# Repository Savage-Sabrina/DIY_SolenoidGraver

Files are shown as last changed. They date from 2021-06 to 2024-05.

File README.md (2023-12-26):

# GraverController
An Arduino Nano based Mosfet controller for solenoid graver.

I got into jewelry making in 2010 to pay for my college expenses. After graduating as a mechanical engineer I realized part of my knowledge should not be wasted and should be applied into something I like.
After looking into the options on a pneumatic graver I realized it was either too expensive or bulky. 
I would not have space for a compressor because I lived in a small room on a shared house.
This is, then, my approach to a solenoid based graver machine.
You could check other approaches like https://github.com/alastair-duncan/SuperEZGraver,  https://www.youtube.com/channel/UCE2rGFm1-xs-WIEHfY1enjA and also my favorite interface https://github.com/Billiam/gravedriver.

The focus I want to bring is of a solenoid for stone setting and fine work, although the power is only limited by the solenoid chosen, buck converter and MOSFET.
You can check videos of it working on [YouTube](https://www.youtube.com/user/selvalss/videos) and the results I got with it [here](https://youtu.be/fjaF6JF7hFk). All tests were performed in the Direct Mode, as programmed in the _Controller_ section below.

If you are handy in terms of Arduino coding and making breadboard circuits this will be super easy to make and program, this will cover mainly a way to make the controller and handpiece with hobby parts. There is also the option to build a custom board with everything integrated already, which is inside the [custom board folder.](https://github.com/Savage-Sabrina/DIY_SolenoidGraver/tree/master/Schematic/Custom%20board%V2) This last option has the benefit of being tidy and you have also all the 3d files to make it look good and functionally tested.

# **Starting the project**
I am sharing this to provide more information on what might be necessary to build your own solenoid engraving machine.

With this I assume that you are:

1. Old enough to know your limitations
1. Liable to your own choices
1. Knowledgeable in electronics

None of the links shared in this guide are affiliate links.

The intent with this guide is to provide knowledge and maybe a bit of opportunity to those who cannot afford a commercial machine or do not have access to the means necessary to get hold of one. I know how it feels to “plan” to buy a machine if we save 50% of our income for the next 5 years to be able to afford the basic version without accessories to run it. No infringement of copyright or patent is intended.

---
# **The solenoid**
The solenoid used should be strong enough to provide the magnetic field but light enough not to be bulky and on the way when engraving. The voltage rating as well as the duty cycle should be compatible with the usage.

A better solution would be to have a commercially available solenoid as the impact source, this would provide some maintenance possibilities. A good choice would be the 12V version of the solenoid 1335. [ITS-LZ-1335-D-24VDC](https://www.elpro.org/gb/red-magnetics-its-lz-series/32677-its-lz-1335-d-24vdc.html) solenoid (The name 1335 means 13mm X 35mm, some companies use the 13x27 which disconsiders the thread length).

The disadvantage of this solenoid is that the diameter of the impact shaft will make it crooked after approx. 300h of use in maximum load (based on tests with impact on an upstanding weight of 40 grams), which is reasonably long but not something to be disregarded.

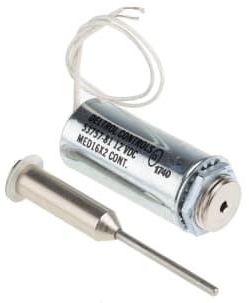
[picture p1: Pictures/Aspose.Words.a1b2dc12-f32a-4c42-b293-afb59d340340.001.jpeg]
53757-81 | Deltrol Linear Solenoid, 12 V dc, 35.9N, 1.4 (Stroke N @ 0.75 in), 25.4 (Dia.) x 60.33 mm | RS
ITS-LZ 1335-D – RED MAGNETICS

Another disadvantage of this model is that the solenoid cannot release enough heat and might overheat, solutions to this are:

1. Make a heatsink for it.
2. Manufacture an open handpiece to allow airflow.
3. Usage of a [Flyback Diode](https://en.wikipedia.org/wiki/Flyback_diode) to remove voltage spikes from the coils. **(This one is actually mandatory)**

## **Custom Solenoid**
If you intend to produce your own solenoid there are some considerations that should be put in place that will make your life easier:

1. The plunger for the solenoid should be floating so as to regulate the amplitude of the impact, a smaller amplitude can lead to faster and more delicate impacts, a greater amplitude can be good for the bezel setting or steel engraving. Free floating solenoids like the 1335 above are regulated by putting some limiter in the back to reduce or increase its amplitude like some sort of screw.
1. The plunger weight should be around 6-8 grams to allow flexibility of energy and speed. A 6 g plunger with the right spring and coil can get up to 60 HZ with an amplitude of 3mm. An 8 gram plunger can even engrave steel, with a 5mm amplitude.
1. An open design of the coil to dissipate the heat will make it last and allow it to use the handpiece for longer since it won’t be too hot.
1. Do not forget the flyback diode as mentioned before.
1. Make sure the wire for the coil can handle the voltage and current to avoid melting and increased temperature.

A plunger with the dimensions below and a handmade spring with a 0.2mm wire can yield great results. The advantage of this is to manufacture something that is exclusive to your needs. With these dimensions I was able to engrave steel and also fine tune it to set 1.3mm stones pave style. The 0.7 mm step is the place to fit the spring, this solenoid should be powered at 12V 25% duty cycle maximun.



---
# **The handpiece**
After some iterations and failures I want to bring some insights to the design if you want to use the one developed or project your own.



For a design that can be assembled with minimal tools and an optional 3d printer you can check my page. The good thing about being open is that we can be sure that people will create better options than our own idea.



This design allows you to use a 1335 solenoid and a 9/16 inch brass tube from K&S to enhance the structure of the parts. The tube that fits the [GRS tool holder](https://grs.com/product/grs-quickchange-handle/) is a [5/16 inch tube from K&S metals](https://ksmetals.com/products/br029-5-16?_pos=1&_psq=5%2F16&_ss=e&_v=1.0), it can be used as a sleeve to make the plast stronger and for the collet to slide easier. If you want to make your own design this tube fits in a 3d printed hole of 7.2mm better due to the approximation of a circle to a polygon.
For a better fit, with some adjustments, the standard tube 3/8" 16 gauge will have a tight grip on the GRS collet. Although not ideal it can be sanded up to the allow movement when hit. The tube can be found on steel, which is a bit harder to work but more durable, or brass.
Some other options can be considered, like using machining services offered online for a perfect fit with the internal dimension of 1/4" or 6.35 mm. With this approach you can not only make your own handpiece but also your own quick change handle. The sleeve should look like the image below.

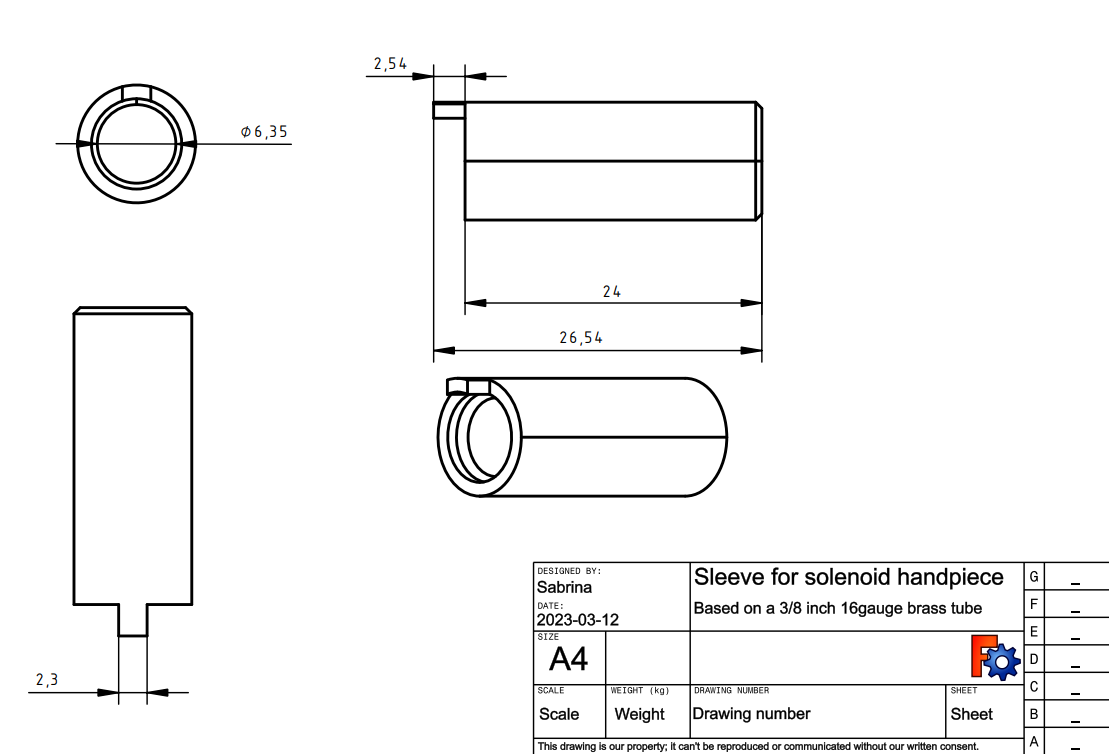
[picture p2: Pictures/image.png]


This thicker sleeve would replace the thin K&S Tube pirctured below. I got better results with this snaded version of the brass tube.

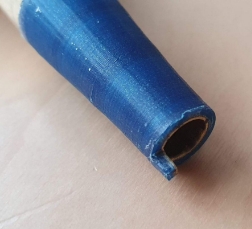
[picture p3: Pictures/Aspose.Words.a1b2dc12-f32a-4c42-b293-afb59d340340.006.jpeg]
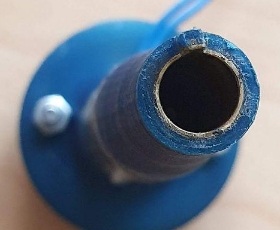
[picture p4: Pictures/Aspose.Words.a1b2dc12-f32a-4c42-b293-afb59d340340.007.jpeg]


---
# **Controller**
For the controller I went with 2 different platforms, one with a Raspberry PI PICO to have a touch interface and better PWM controls and an Arduino to make things cheaper and accessible to the majority of people. I projected a custom board that contains all the components in one, the board is only aimed at people that really know what they are doing, you can find it in the [custom board folder](https://github.com/Savage-Sabrina/DIY_SolenoidGraver/tree/master/Schematic/Custom%20Board%20V2)

In this document I will handle only the Arduino version of the controller as it is the simplest and readily available. For the Raspberry version I realized that the version of the software installed as well as the version of MicroPython impacted on the controls and had some bugs and differences due to the GPIO.PWM frequency limitations. The parts referenced are just a guideline, they are not exclusive or irreplaceable.

Necessary parts:

1. Arduino (The cheapest one that will work is the [Nano](https://store.arduino.cc/products/arduino-nano), since it’s an open platform you can use a “generic” version)
1. [Mosfet board](https://www.amazon.com/HiLetgo-IRF520-MOSFET-Arduino-Raspberry/dp/B01I1J14MO) (Learn more about MOSFETS [Here](https://dronebotworkshop.com/transistors-mosfets/))
1. Expression pedal ([This](https://www.thomann.de/se/maudio_expression_pedal.htm) was the cheapest in Europe and worked like a charm)
   1. Or a [potentiometer pedal](https://thepihut.com/products/foot-pedal-potentiometer-sewing-machine-speed-controller).
1. PSU (A laptop PSU can fulfill the needs of almost everyone, I could even engrave steel with a 18V 4A)
1. 2X [Potentiometers](https://thepihut.com/products/gravity-analog-rotation-potentiometer-sensor-v1-for-arduino)

Optional parts:

1. [Buck converter](https://thepihut.com/products/dc-dc-power-module-25w) or [this](https://www.amazon.ca/Lysignal-LM2596-Supply-Adjustable-Converter/dp/B074J4NXCM), Make sure the output voltage is set to 5V before you connect the components (Makes only one PSU enough instead of 2 connectors)
1. [Buttons](https://thepihut.com/products/stemma-wired-tactile-push-button-pack-5-color-pack) (If you are going for a more complete programming they are necessary)
1. [Switch](https://thepihut.com/products/mini-panel-mount-dpdt-toggle-switch) (To make it easier to turn the power from the PSU on and off)
1. [Breadboard](https://thepihut.com/products/raspberry-pi-breadboard-half-size) (Makes it easier to connect the wires)

For the Arduino pinout any variant can be used. The model represented in the schematics is the Arduino Nano.

The schematics of the connection is as shown below:



The complete schematics are [in the shared folder](https://github.com/Savage-Sabrina/DIY_SolenoidGraver/tree/master/Schematic) with a .PDF or .PNG file.

What has to be done when assembling it safelly:

1. Check if all the connections are in place apart from the PSU.
1. Connect the Arduino to the pc and use the ArduinoIDE interface to check the code.
1. Upload the [Arduino code](https://github.com/Savage-Sabrina/DIY_SolenoidGraver/blob/34cf9a5d53c3de1b95fa2ae14cb3af24335a9292/Arduino%20Code/BetaVersion0.2LCD+VariableFootPedal.ino) for the desired control, which will have 3 modes:
   1. Frequency mode, you choose the frequency and the duty cycle with the potentiometers, the pedal will change the power input according to the selection, the information is shown on the LCD.
   1. Pulse mode, the handpiece will give a certain amount of pulses according to frequency and duty, the pulses go to maximum power at start and stop for half a second then continue within a defined interval.
   1. Direct mode, the handpiece goes to maximum power instantaneously according to duty and frequency selected.
1. Test the board without the solenoid handpiece or PSU in place and look at the LED of the mosfet to look for it blinking.
2. Use a weaker PSU just to check the main connections.
3. Assemble everything and test it for a split second to verify short circuits in your assembled handpiece. To avoid heating of the handpiece don't forget the Flyback diode.
4. Enjoy!

---
# **Custom board V2**
The custom board below has already the connections made and it's only up to you to connect the power lines, pedal, graver and your own Arduino Nano. You can order the boards on PCB manufacturers that send it to the whole world like PCBWay and JLCPcb.
You can find the design on the [custom board folder.](https://github.com/Savage-Sabrina/DIY_SolenoidGraver/tree/master/Schematic/Custom%20Board%20V2)
The design is divided in 2 parts, the Arduino Nano Board and the Controll Board with buttons and potentiometers as shown below:
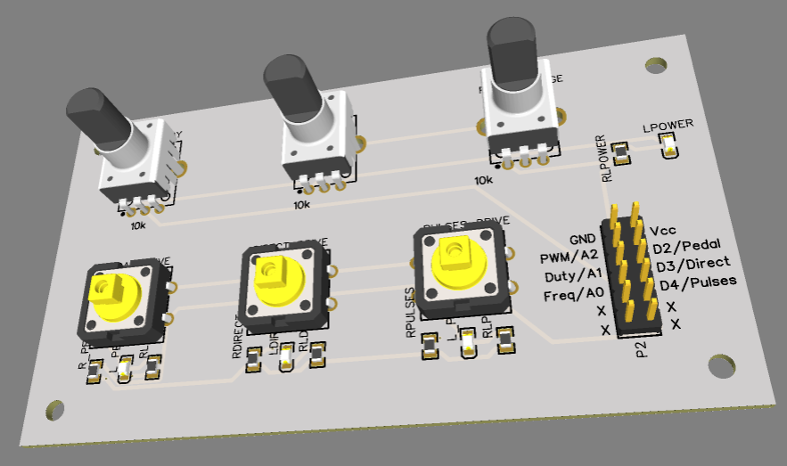
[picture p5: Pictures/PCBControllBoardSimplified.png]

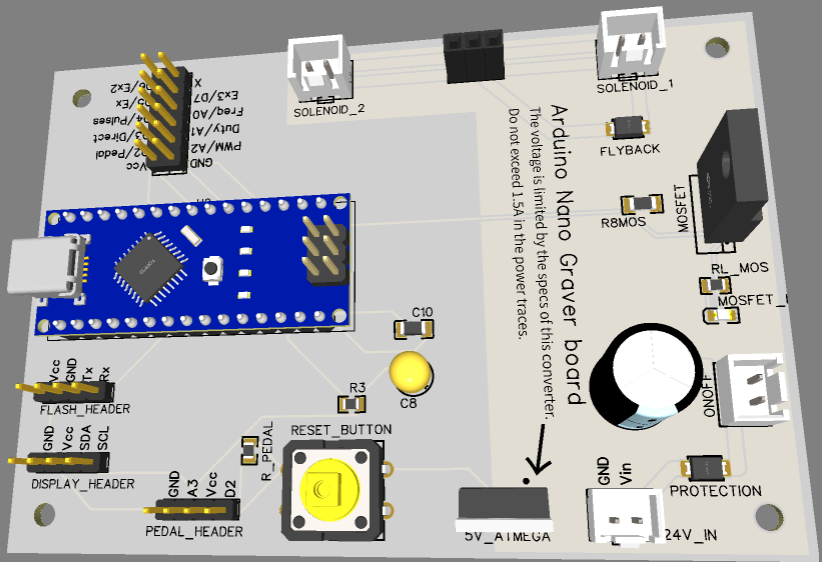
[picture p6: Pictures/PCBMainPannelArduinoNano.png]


***
# **Final considerations**

If you feel that something should be changed or is wrong feel free to inform me or to perform your own modifications.
Suggestions are always welcome, I had a brief contact with a professional grade engraver in order to feel the impact in the hand and tool behavior which was not enough to feel the nuances of the machine.
If you need assistance with the project please message me on reddit u/Weird\_Singularity.

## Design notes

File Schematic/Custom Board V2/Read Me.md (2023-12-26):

This version of the board is the final developed for the Arduino Nano.
I realized that not everyone had the knowledge to burn a bootloader on the MCU so the arduino Nano option was the best option.
The board can handle the 18V 1.5A on the power traces.
The code is on the Arduino Code folder in a way that is shown on the youtube video.

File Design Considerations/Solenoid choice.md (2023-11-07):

For a full in depth review of the solenoid choices please watch the video about the perks and configuration of each magnet below. [Youtube video about the solenoids and handpiece](https://www.youtube.com/watch?v=2lFhfABcx04)

The first solenoid I tested was the smallest 5v solenoid i could get just to prove the concept. [Small solenoid](https://www.adafruit.com/product/2776)
small 5V solenoid

It was really weak and I realized that I was supposed to know about how a graver would work.
I found some options to understand better the impact force on this video from [Shaun Hughes](https://www.youtube.com/watch?v=1zzqaAYdvdQ&ab_channel=ShaunHughesEngraving) and from that went on the look for a solenoid that would give me the aproximate ammount of travel for this to happen.

The first solenoid I went to was a popular [jf-0530B](https://www.aliexpress.com/item/32777233179.html) (12V, 300mA) that had quite a punch but a long stroke and long body, making the handpice too bulky. Maybe to replace a hammer and chisel for someone with a hand disabilyty might be awesome.
jf-0530b

The second solenoid used was the one from [Adafruit](https://www.adafruit.com/product/413),with 12V and 250mA it was a little wider. It had strong strokes but a lower frequency of oscilation. (https://www.adafruit.com/product/413)
adafruit solenoid

I had an intermediary solenoid (12V, ~900mA) that was open and could dissipate better the heat while having a good impact force. Like the on on the [link](https://www.aliexpress.com/item/4000013441378.html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,searchweb201602_,searchweb201603_), unfortunatelly this also had a low frequency and to make it fit on an easy handpiece was a hassle.

Used a [linear cylindrical solenoid](https://www.red-magnetics.com/en/product-groups/linear-solenoids/cylinder-solenoids/its-lz-1335-d/) to have better control on the stroke length and natural frequency of the solenoid. Got this one on the 12V and 24V variants. After testing for some time I realized my tolerances were too tight as the shaft had bended and shortened with the impact. I would need something more robust as an impact shaft to withstand the continuous impacts on the solenoid.

I had to find an intermitent duty, 12-24V solenoid that would be good to use and easy to maintain. Found a [perfect match](https://www.youtube.com/watch?v=ASwVTQaLLGc&t=62s&ab_channel=IndexBraille) with no avail to get my hands on it as the complay would not sell unless I had the machine that would use it. So I had to find something similar on the internet. After going back and forth with the manufacturer I got a [replacement solenoid](https://www.aliexpress.com/item/32996508114.html?spm=a2g0s.9042311.0.0.53844c4ddj9pqp) that would be the same function as the perfect match I wanted. Cut the shaft to length and got a better frequency of oscilation on the solenoid and better impact force with 19V. But it would still overheat. Thats were I came to realization that it's better to make my own solenoid. The saft from the cheap solenoid is percet to make my own. And this is the next step on the making of the handpiece.


Extras:
How to make a solenoid: https://www.instructables.com/How-to-Make-Solenoid-at-Home/
Mosfet control for NERF: https://www.youtube.com/watch?v=hRxzcRwo_3U&ab_channel=Valour%27sBlasters

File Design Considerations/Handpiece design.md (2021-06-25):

To start the desig of thehandpiece I took into consideration the design of current pneumatic gravers. To keep standard dimensions went first on some commercial models, [technical drawings](https://www.chipmaker.ru/topic/132834/?page=4) and details I found on some [forums](https://www.jportal.ru/forum/forum76/topic15895/).
I will skip here the previous considerations of the handpiece from the solenoid choice on the other folder of this project, therefore I will only cite here the design based on the last solenoid.

1 - The easiest collet to use.
2 - The strength of the connection from the 3D printed version to the piston tube.
3 - Heat dissipation.
4 - Possibility of control the stroke lenght on a free piston solenoid.

1 - The easiest collet to use that was [available](https://www.cooksongold.com/Jewellery-Tools/GRS-Quick-Change-Traditional-Tool-Holder-For-3.45mm-Shank-Gravers----Pack-of-3-prcode-998-G231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) was the GRS collet that had 6.35mm diameter or 1/4 inch. (I don't like these imperial measurements I would rather have a collet with a round mm number that would make it easier to adapt something) I had it available on my country since it's a global and present company.

2 - To resolve the strengh of the connection on the plastic of the 3D printed handpiece, avoiding it breaking because of the constant impact and rubbing on the plastic, I found online a [hobbist brass tube](https://www.hobbylinc.com/k-s-round-brass-tube-9:32-hobby-and-craft-metal-tubing-8132) with the correct internal diameter matching the external diameter of the collet. This way I would insert the brass tube inside the 3D printed handpiece to hold the collet and make a smoother movement while also strenghtening the handpiece on the most critical place.

3 - Heat dissipation would be done by having openings on the faces that had the least ammount of stress. Since the PLA used would retain the heat it would not be good to have it carry the heat away. For now the heat will go to all he sides instead of a channeled air path.

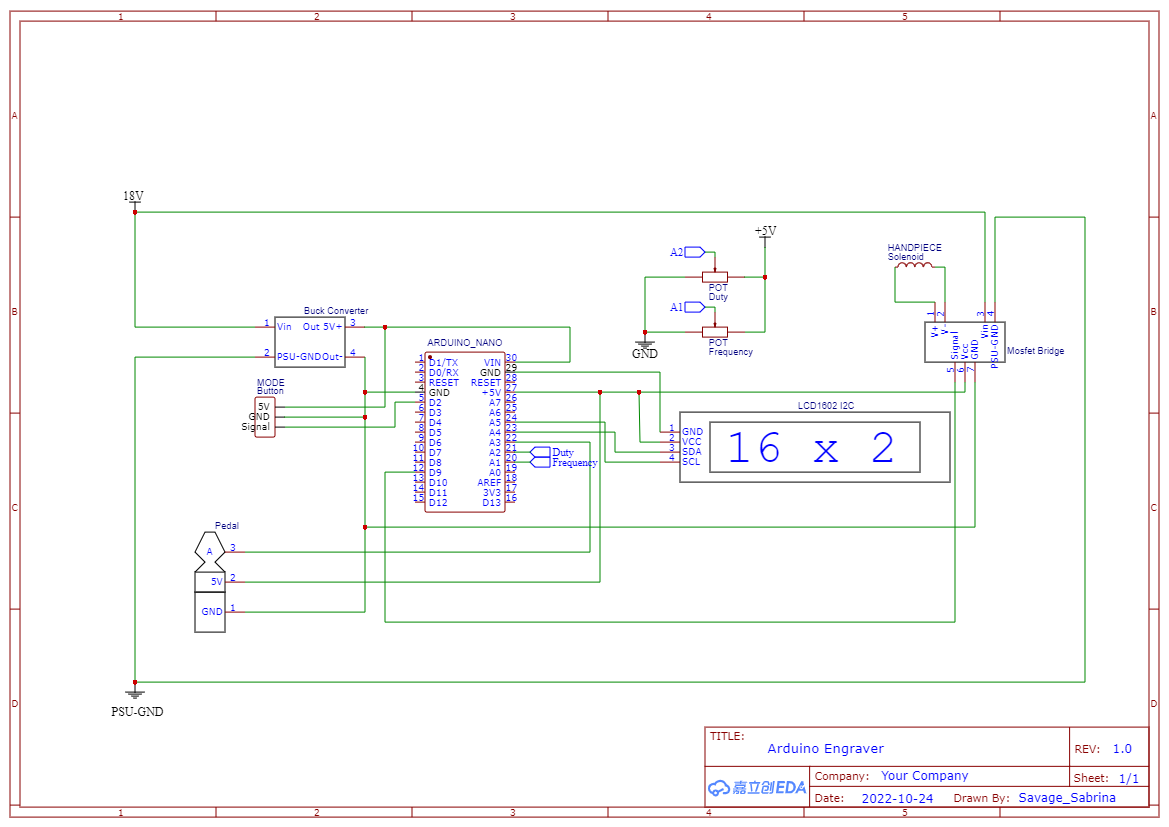
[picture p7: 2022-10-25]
Schematic/Schematic_ArduinoNanoEngraver_2022-10-24.png

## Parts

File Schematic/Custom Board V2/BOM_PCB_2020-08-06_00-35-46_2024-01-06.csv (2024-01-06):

ID | Name | Designator | Footprint | Quantity | Manufacturer Part | Manufacturer | Supplier | Supplier Part | Price | Pins | 3DModel | Contributor | LCSC Assembly | SMT Type | image | link
1 | 17-21SUYC/TR8 | LDIRECT,L_PEDALDRIVE,L_PULSES,LPOWER | LED0805-RD | 4 | 17-21SUYC/TR8 | KENTO | LCSC | C2296 | 0.012 | 2 | LED0805-RD | lcsc | Yes | Basic | //image.lceda.cn/szlcsc/C2296.jpg | https://item.szlcsc.com/255094.html
2 | 1K | RDIRECT,RPULSES,R_PEDALDRIVE | R0805 | 3 | 0805W8F1001T5E | UniOhm | LCSC | C17513 | 0.002 | 2 | R0805_L2.0-W1.3-H0.6 | layout | Yes | Basic |  | https://item.szlcsc.com/142685.html
3 | 75 | RLDIRECT,RLPEDALDRIVE,RLPULSES | R0805 | 3 | 0805W8F750JT5E | UniOhm | LCSC | C20638 |  | 2 | R0805_L2.0-W1.3-H0.6 | layout | Yes | Basic |  | https://item.szlcsc.com/142685.html
4 | 10K | DUTY,FREQUENCY,PWM/VOLTAGE | RES-TH_RK09K1130AAU | 3 | RK09K1130AAU | ALPS Electric | LCSC | C202373 | 0.624 | 5 | RES-TH_RK09K1130AAU | LCSC |  |  |  | https://list.szlcsc.com/catalog/556.html
5 | B3F-4055 | DIRECT_DRIVE,PEDAL_DRIVE,PULSES_DRIVE | KEY-TH_4P-L12.0-W12.0-P5.00-LS13.4-EH | 3 | B3F-4055 | OMRON | LCSC | C84931 | 0.088 | 4 | KEY-TH_4P-L12.0-W12.0-H7.5-LS12.5-P5.0 | lcsc |  |  |  | https://item.szlcsc.com/84377.html
6 | Header-Male-2.54_2x6 | P2 | HDR-TH_12P-P2.54-V-M-R2-C6-S2.54 | 1 |  |  | LCSC | C66689 | 0.038 | 12 | HDR2.54-M-LI-2X6P | lcsc |  |  |  | https://lcsc.com/eda_search?q=C66689&%26type=1&ref=editor
7 | 75 | RLPOWER | R0805 | 1 | 0805W8F750JT5E | UniOhm | LCSC | C20638 |  | 2 |  |  | Yes | Basic

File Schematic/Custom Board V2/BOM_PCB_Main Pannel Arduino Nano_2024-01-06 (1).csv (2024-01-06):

ID | Name | Designator | Footprint | Quantity | Manufacturer Part | Manufacturer | Supplier | Supplier Part | Price | Pins | 3DModel | Contributor | JLCPCB Part Class | LCSC Assembly | SMT Type | image | link
1 | ARDUINO_NANO | U2 | COMM-TH_ARDUINO_NANO | 1 | ARDUINO_NANO | null | LCSC | C9900017879 |  | 30 | ARDUINO_NANO | lcsc | Extended Part |  |  |  | https://lcsc.com/eda_search?q=C9900017879&%26type=1&ref=editor
2 | L7805ACV | 5V_ATMEGA | TO-220-3_L10.0-W4.5-P2.54-T | 1 | L7805ACV | ST(意法半导体) | LCSC | C192854 | 0.352 | 3 | TO-220-3_L10.0-W4.5-P2.54 | LCSC | Extended Part |  |  |  | https://item.szlcsc.com/88574.html
3 | XHB-2A Connector | 24V_IN,ONOFF,SOLENOID_1,SOLENOID_2 | CONN-TH_XHB-2A | 4 | XHB-2A Connector | BOOMELE | LCSC | C57981 | 0.01 | 2 | CONN-TH_XHB-2A | 立创EDA官方封装库 |  |  |  | //image.lceda.cn/szlcsc/C57981.jpg | https://item.szlcsc.com/59018.html
4 | 100nF | C10 | C1206 | 1 | CL31B104KBCNNNC | SAMSUNG | LCSC | C24497 | 0.014 | 2 | C1206_L3.2-W1.6-H1.3 | layout |  | Yes | Basic |  | https://item.szlcsc.com/89171.html
5 | 10uF | C8 | CAP-TH_BD5.0-P2.5-D0.5-FD | 1 | C10uF63V2.5mm5x11mm | ReliaPro | LCSC | C32455 | 0.015 | 2 | CAP-TH_BD5.0-H7.5-P2.5 | lcsc |  |  |  |  | https://item.szlcsc.com/292492.html
6 | 100uF | C9 | CAP-TH_BD10.0-P5.00-D1.0-FD | 1 | 10X17 100V100uf | ValuePro | LCSC | C3336 | 0.092 | 2 | CAP-TH_D10.0-H16.0-P5.00 | lcsc |  |  |  |  | https://item.szlcsc.com/44833.html
7 | Header-Male-2.54_1x4_C124378 | DISPLAY_HEADER,FLASH_HEADER,PEDAL_HEADER | HDR-TH_4P-P2.54-V | 3 | 210S-1*4P L=11.6MMGold-plated black | Ckmtw | LCSC | C124378 | 0.04 | 4 | HDR-M-2.54_1x4 | LCSC |  |  |  |  | https://lcsc.com/product-detail/Pin-Header-Female-Header_Made-in-China-Made-in-China-Headers-Pins1-4-pitch2-54mm_C59481.html
8 | 1N4004F | FLYBACK,PROTECTION | SMAF_L3.5-W2.6-LS4.7-RD | 2 | 1N4004F | SK | LCSC | C122842 | 0.006 | 2 | SMAF_L3.5-W2.6-H1.2-LS4.7 | 官方封装库 |  | Yes | Extend |  | https://item.szlcsc.com/125168.html
9 | IRL520PBF | MOSFET | ITO-220AB-3_L10.2-W4.5-P2.60-L | 1 | IRL520PBF | VISHAY | LCSC | C145199 | 1.316 | 3 | ITO-220AB-3_L10.2-W4.5-H15.0-P2.60 | LCSC |  |  |  |  | https://item.szlcsc.com/387411.html
10 | Header-Female-2.54_1x3 | P1 | HDR-TH_3P-P2.54-V-F | 1 | 2.54-1*3P母 | BOOMELE(博穆精密) | LCSC | C146243 | 0.057 | 3 | HDR2.54-F-LI-1X3P | lcsc | Extended Part |  |  |  | https://lcsc.com/eda_search?q=C146243&%26type=1&ref=editor
11 | 10K | R3 | R0805 | 1 | 0805W8F1002T5E | UniOhm | LCSC | C17414 | 0.001 | 2 | R0805_L2.0-W1.3-H0.6 | layout |  | Yes | Basic |  | https://item.szlcsc.com/142685.html
12 | 75 | RL_MOS | R0805 | 1 | 0805W8F750JT5E | UniOhm | LCSC | C20638 |  | 2 | R0805_L2.0-W1.3-H0.6 | layout |  | Yes | Basic |  | https://item.szlcsc.com/142685.html
13 | 1K | R_PEDAL | R0805 | 1 | 0805W8F1001T5E | UniOhm | LCSC | C17513 | 0.002 | 2 | R0805_L2.0-W1.3-H0.6 | layout |  | Yes | Basic |  | https://item.szlcsc.com/142685.html
14 | 1K | R8MOS | R1206 | 1 | 1206W4F1001T5E | UniOhm | LCSC | C4410 | 0.003 | 2 | R1206_L3.2-W1.6-H0.6 | layout |  | Yes | Basic |  | https://item.szlcsc.com/311874.html
15 | B3F-4055 | RESET_BUTTON | KEY-TH_4P-L12.0-W12.0-P5.00-LS13.4-EH | 1 | B3F-4055 | OMRON | LCSC | C84931 | 0.088 | 4 | KEY-TH_4P-L12.0-W12.0-H7.5-LS12.5-P5.0 | lcsc |  |  |  |  | https://item.szlcsc.com/84377.html
16 | 17-21SUYC/TR8 | MOSFET_L | LED0805-RD | 1 | 17-21SUYC/TR8 | KENTO | LCSC | C2296 | 0.012 | 2 | LED0805-RD | lcsc |  | Yes | Basic | //image.lceda.cn/szlcsc/C2296.jpg | https://item.szlcsc.com/255094.html
17 | Header-Male-2.54_2x6 | P2 | HDR-TH_12P-P2.54-V-M-R2-C6-S2.54 | 1 |  |  | LCSC | C66689 | 0.038 | 12 | HDR2.54-M-LI-2X6P | lcsc |  |  |  |  | https://lcsc.com/eda_search?q=C66689&%26type=1&ref=editor

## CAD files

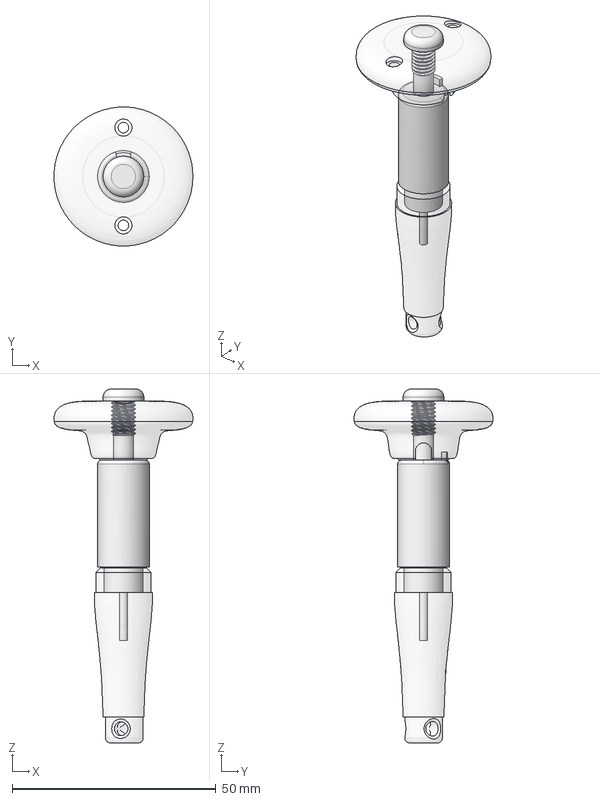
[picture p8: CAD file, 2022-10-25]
CAD files/Assembly new handpiece 1335.FCStd
34.1 x 34.1 x 86.9 mm
Solenoid 1335_001
Collet GRS_001
Front cap_001
BackBody Part_001
Back Lid Part_001
Screw cap_001

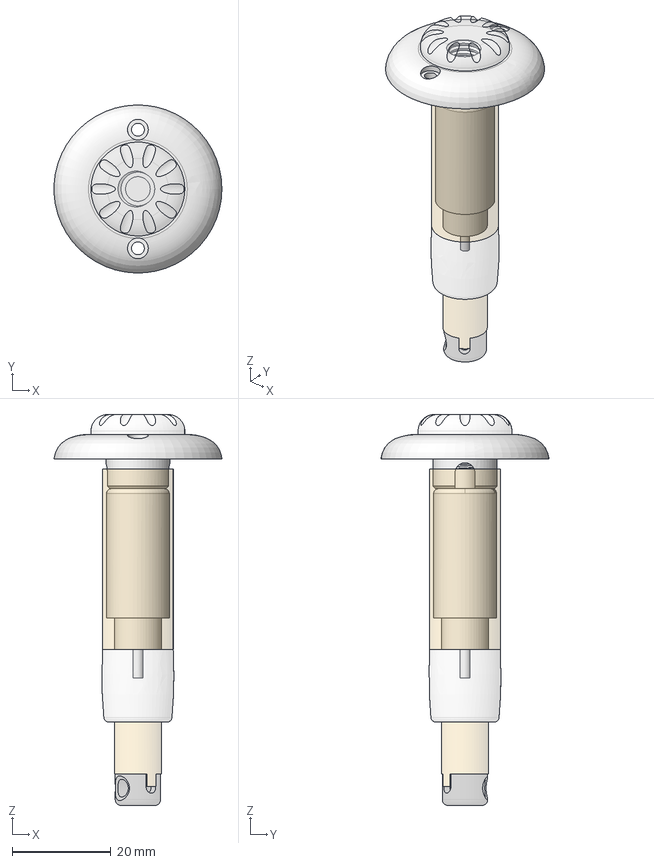
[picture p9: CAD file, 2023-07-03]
CAD files/Thick sleeve/Assembly new handpiece 1335.FCStd
34.0 x 34.0 x 79.1 mm
Solenoid 1335_001
Collet GRS_001
Back Lid Part_001
Front cap thick sleeve_001
3 8 inch sleeve_001
Screw cap_001
Tube_001

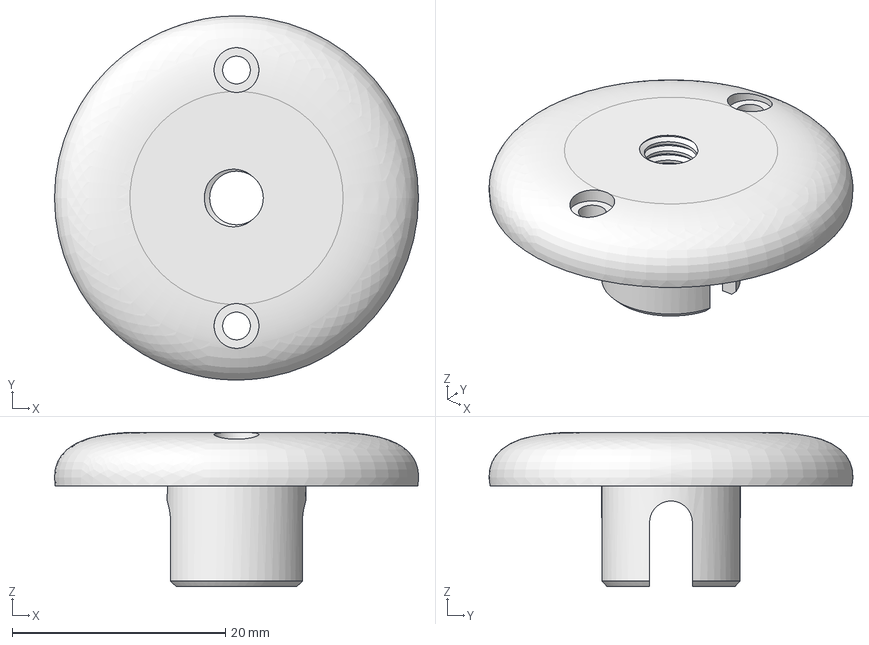
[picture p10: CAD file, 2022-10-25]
CAD files/Back Lid Part.FCStd
34.1 x 34.1 x 14.5 mm

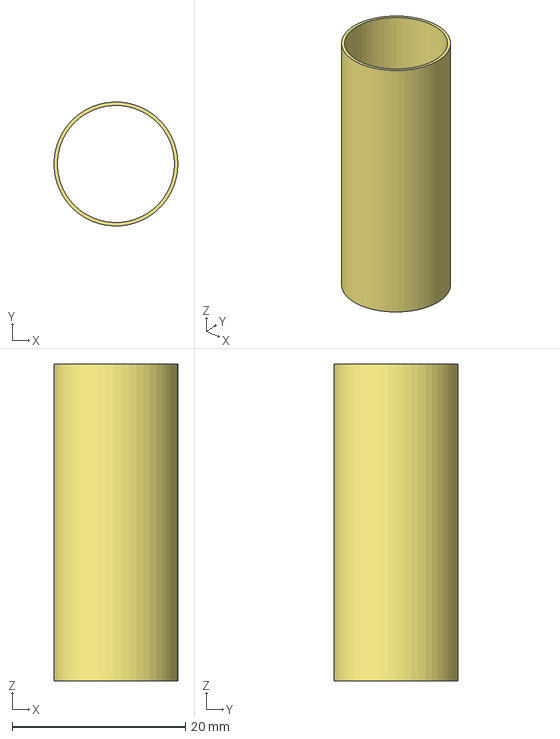
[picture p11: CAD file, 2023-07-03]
CAD files/Thick sleeve/Tube.FCStd
14.3 x 14.3 x 36.5 mm

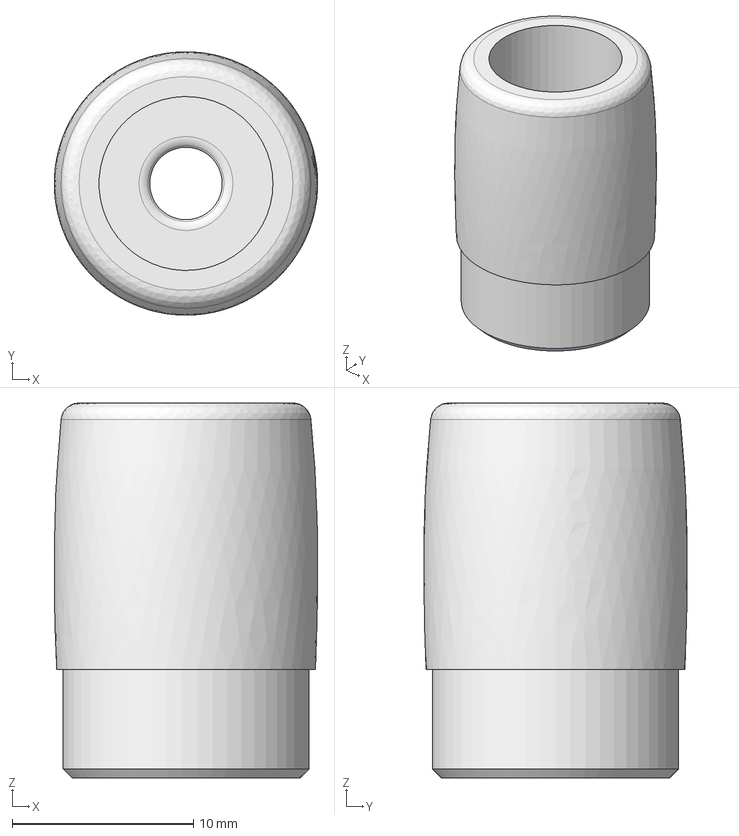
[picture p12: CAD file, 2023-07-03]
CAD files/Thick sleeve/Front cap thick sleeve.FCStd
14.5 x 14.5 x 20.7 mm

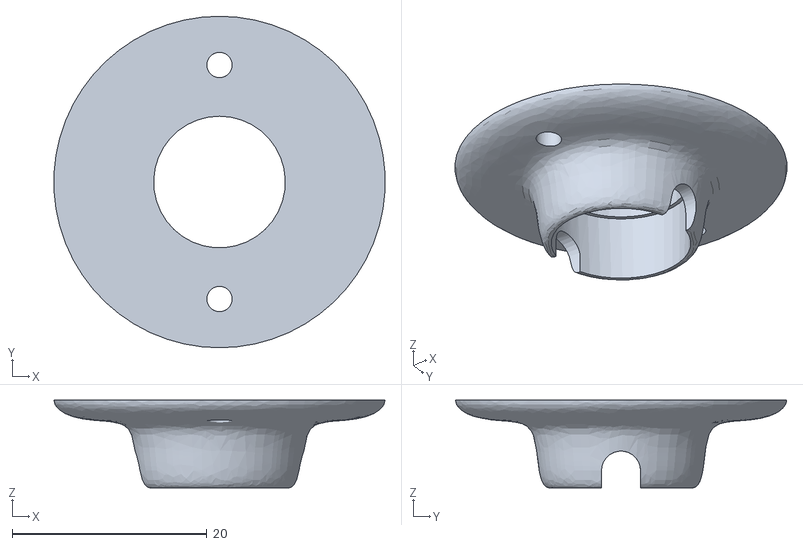
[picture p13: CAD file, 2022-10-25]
CAD files/BackBody Part-Body.stl
34.0 x 34.0 x 9.01

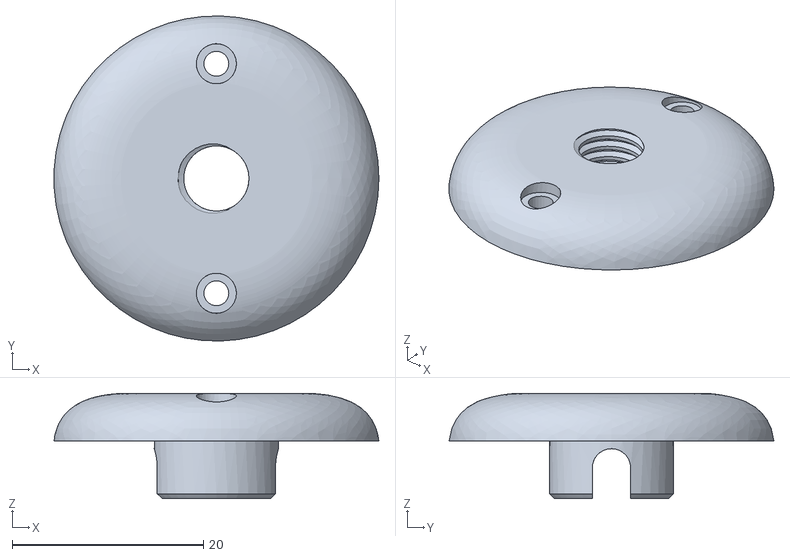
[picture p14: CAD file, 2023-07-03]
CAD files/Thick sleeve/Back Lid Part-Body.stl
34.0 x 34.0 x 11.0

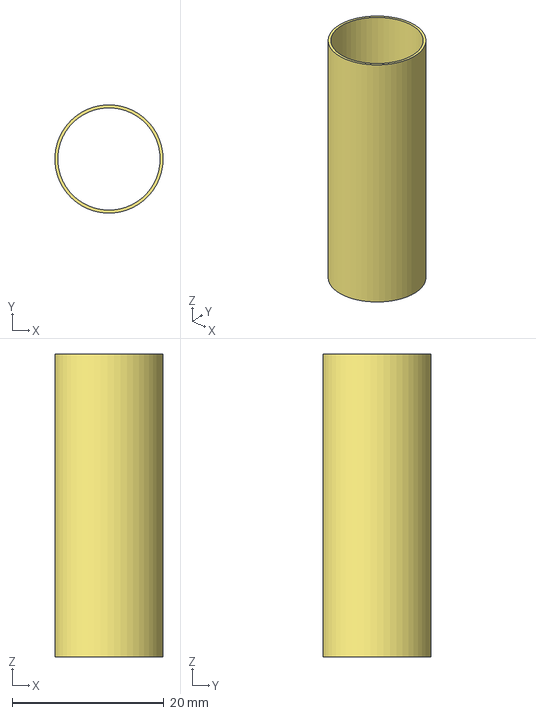
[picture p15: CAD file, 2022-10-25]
CAD files/Tube.FCStd
14.3 x 14.3 x 40.0 mm

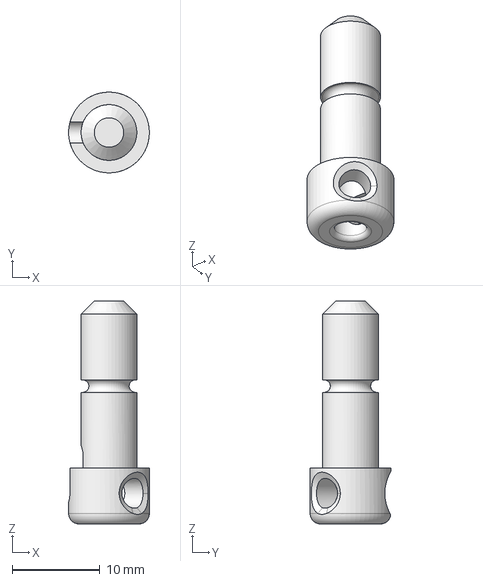
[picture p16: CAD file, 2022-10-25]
CAD files/Collet GRS.FCStd
9.20 x 9.20 x 25.4 mm

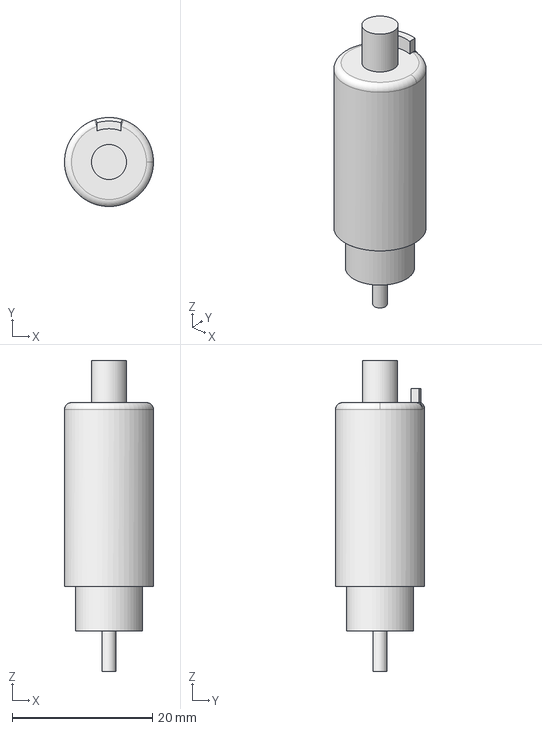
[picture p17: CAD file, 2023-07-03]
CAD files/Thick sleeve/Solenoid 1335.FCStd
12.7 x 12.7 x 44.3 mm

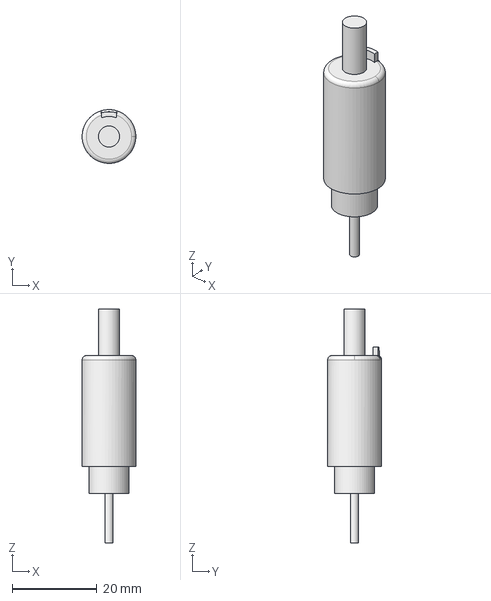
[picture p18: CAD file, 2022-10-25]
CAD files/Solenoid 1335.FCStd
12.7 x 12.7 x 55.2 mm

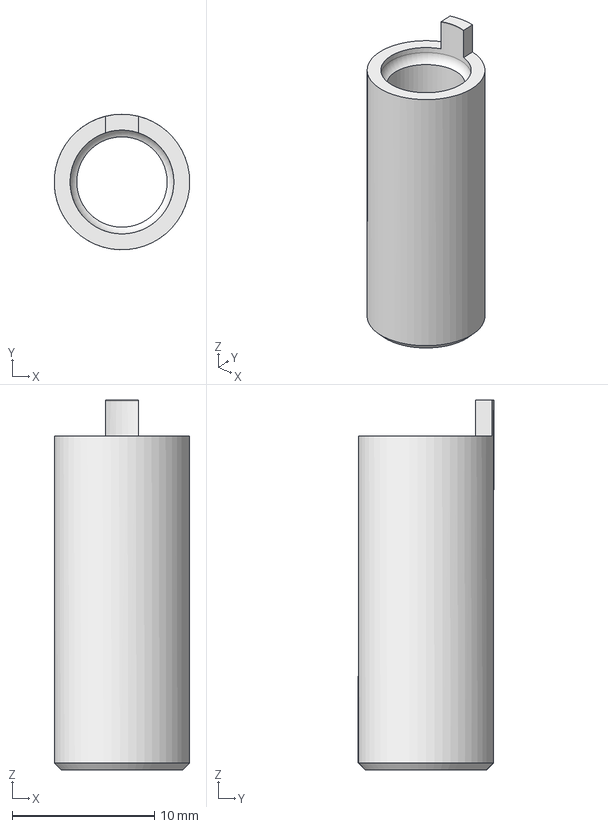
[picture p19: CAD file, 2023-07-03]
CAD files/Thick sleeve/3 8 inch sleeve.FCStd
9.52 x 9.52 x 26.0 mm

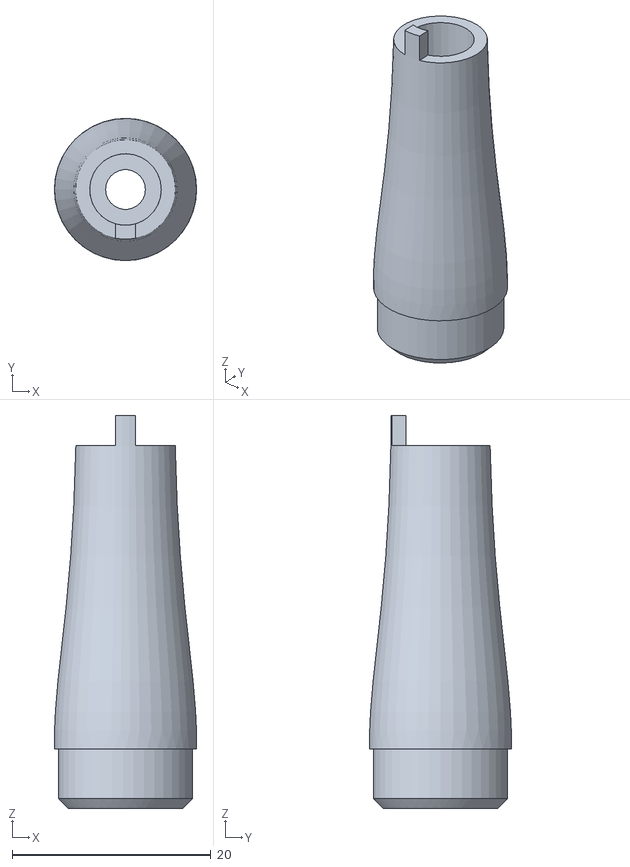
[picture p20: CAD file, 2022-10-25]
CAD files/Thick sleeve/Front cap-Body.stl
14.3 x 14.3 x 39.5

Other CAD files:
CAD files/Thick sleeve/BackBody Part-Body.stl
CAD files/Back Lid Part-Body.stl
CAD files/Thick sleeve/Back Lid Part.FCStd
CAD files/Thick sleeve/Front cap thick sleeve-Body.stl
CAD files/Thick sleeve/BackBody Part.FCStd
CAD files/PreviousIdeas/Adjustment knob-new-custom-solenoid.stl
CAD files/PreviousIdeas/Assembly new handpiece 1335.step
CAD files/PreviousIdeas/Back Lid Part-Body.step
CAD files/PreviousIdeas/Back Lid Part-Body.stl
CAD files/PreviousIdeas/BackBody Part-Body.step
CAD files/PreviousIdeas/BackBody Part.FCStd
CAD files/PreviousIdeas/Cap-Body-new-custom-solenoid.stl
CAD files/PreviousIdeas/Collet GRS-Body.step
CAD files/PreviousIdeas/Front cap-Body.step
CAD files/PreviousIdeas/Front cap.FCStd
CAD files/PreviousIdeas/New Handpiece Custom Solenoid-Body001.stl
CAD files/PreviousIdeas/Screw cap-Body.step
CAD files/PreviousIdeas/Screw cap-Body.stl
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

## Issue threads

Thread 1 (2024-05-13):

STEP files for ease of compatibility?

happycncer, 2024-05-13:
Is there any possibility of having the CAD Files (listed under PreviousIdeas) available in STEP format? I only ask as this can be imported more readily by many other CAD Software products. It's predominately the parts needing to be 3D printed that are the most difficult, as they are mostly all shown in the FreeCad format - which is not particularly friendly when trying to import them into other CAD applications.

Savage-Sabrina, 2024-05-20:
The files were converted and uploaded to the same folder in order to make the compatibility easier.

Closed 2024-05-20.

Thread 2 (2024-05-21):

Gerber files appear incomplete?

Kigurai, 2024-05-21:
Gerber files appear incomplete and wont work on PCBway, etc.

Savage-Sabrina, 2024-05-23:
Uploaded the extracted version used for the production on jlcpcb, only the main components are in place, did not put the buttons, connectors and arduino as they can be a personal preference for the user. Thank you for the attention.

Closed 2024-05-23.

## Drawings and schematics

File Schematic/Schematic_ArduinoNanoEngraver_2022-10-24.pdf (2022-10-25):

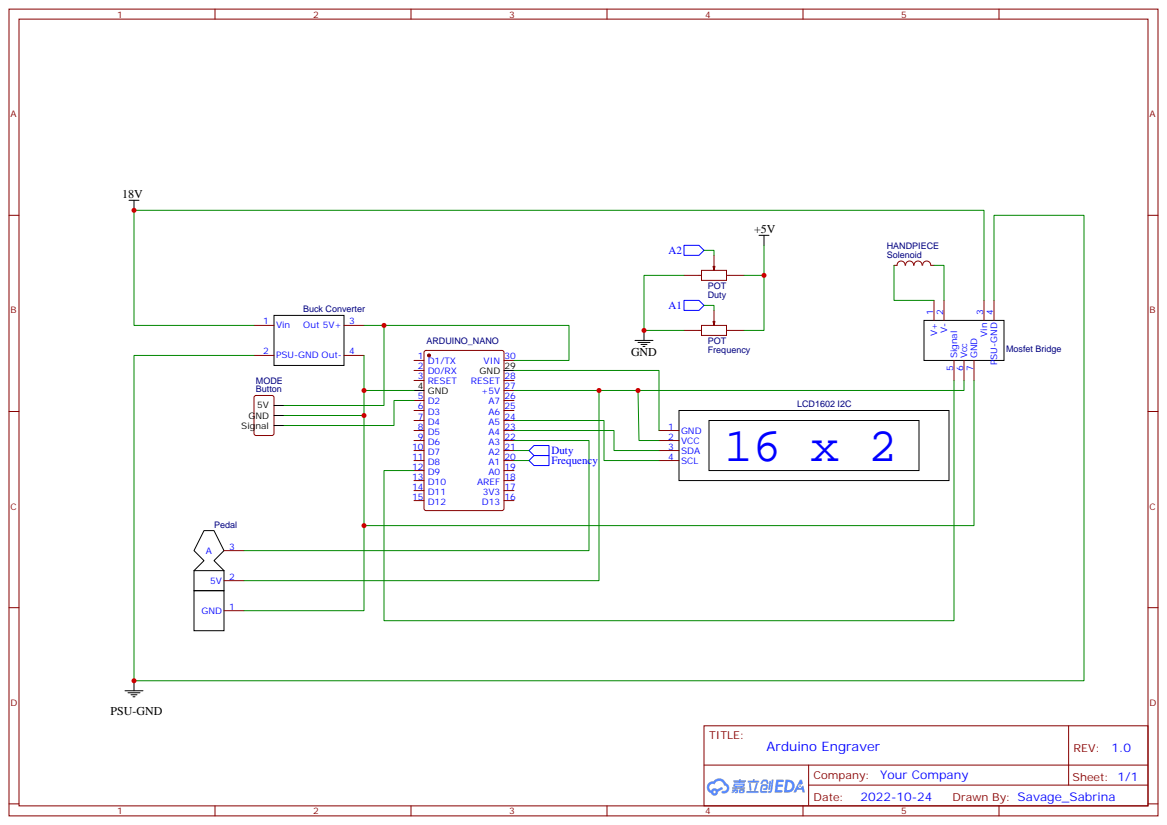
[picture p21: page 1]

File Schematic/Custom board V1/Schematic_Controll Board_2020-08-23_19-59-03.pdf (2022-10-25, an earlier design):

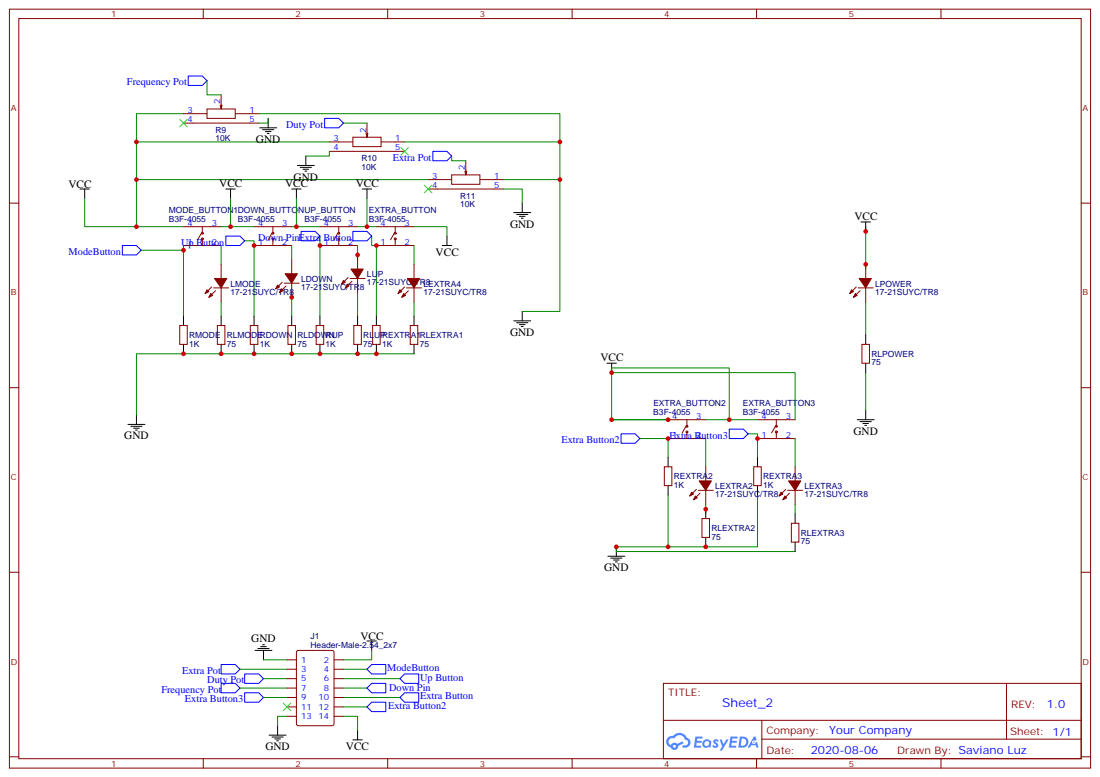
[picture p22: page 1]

Drawn By: Saviano Luz

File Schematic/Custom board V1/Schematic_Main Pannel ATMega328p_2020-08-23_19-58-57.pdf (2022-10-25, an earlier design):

# ICSP

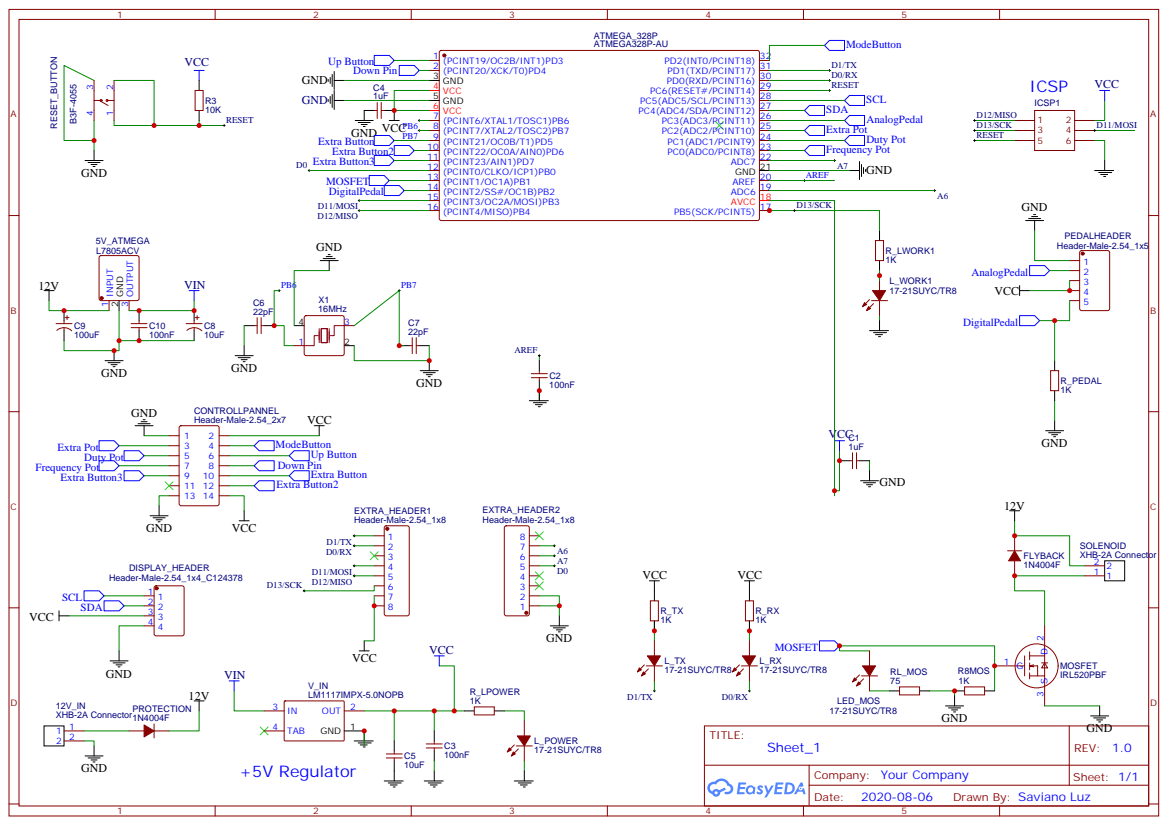
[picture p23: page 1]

Drawn By: Saviano Luz

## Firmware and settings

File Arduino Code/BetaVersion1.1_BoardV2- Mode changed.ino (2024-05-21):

#include <Wire.h> 



//Assingning Analog Pins

const int FrequencyPin = 0;               //Pin that sets the maximun frequency (ANALOG)
const int DutyPin = 1;              //Pin from percentage of the cycle that turns the solenoid on (ANALOG)
const int PWMPin = 2;              //Pin from percentage of the cycle that turns the solenoid on (ANALOG)

//Assigning digital Pins

const int VariablePedalPin = 2;              // Pin to select variable pedal mode (DIGITAL)
const int SelectedInputPin = 3;                //Pin to select potentiometer mode (DIGITAL)
const int PulsesPin = 4;              //Pin to select pulses pedal mode (DIGITAL)
const int MosfetPin = 9;                  // the number of the LED pin (DIGITAL)




//Assigning variables

float PeriodMosfet  = 0;                  //Time between the impacts its a ratio between 1/frequency
float FrequencyMosfet = 1;                //Frequency in hertz of the impacts means impacts per second
float PercentageMosfet = 5;              //Percentage of the cycle that turns the solenoid on
float FootPedal = 0;                      //State of the foot pedal
float AnalogPedal = 0;                    //Defines the analog value of the varible pedal
float TimeForPulses = 1000;               //Base time for pulses on pulse mode
float StartOfPulses;                      //Marker for start of pulses
float DutyRead;                           //Duty cycle
float Correction;                          //Correction value for different solenoids
int DirectFrequency=1;                  //Value for the frequency on direct mode
int PWMValue=0;                   //PWM to correct for lower voltages solenoids.
int MaxFrequency;                   //Maximum frequency for the pedal

int Mode=2;                                 //Mode of action starts at the mode you've defined below 
int MosfetState = LOW;                    //Mosfet state for the action High means activated Low deactivated

int LastVariableState = LOW;
int VariableState;
long LastDebounceMode = 0;                // the last time the output pin was toggled

int LastSelectedInputRead = LOW;
int SelectedInputState;
long LastDebounceSelectedInput = 0;                              

int LastPulsesState = LOW;
int DownState;
long LastDebouncePulses = 0;

long LastDebounceLCD = 0;


unsigned long CurrentTime = 0;
unsigned long PreviousTime = 0;


long debounceDelay = 50;                  // the debounce time; increase if the output flickers



void setup() {
  pinMode(VariablePedalPin, INPUT);          //Button to select the mode
  pinMode (SelectedInputPin, INPUT);
  pinMode(MosfetPin, OUTPUT);             //Set solenoid pin as output to Mosfet

 

  }






void loop() {
  int VariableRead = digitalRead(VariablePedalPin);
  int SelectedInputRead = digitalRead (SelectedInputPin);
  int PulsesRead = digitalRead(PulsesPin);
  
  
  if (VariableRead != LastVariableState) {                  //Reading the state for the Mode Button, function to change the mode of the machine
    // reset the debouncing timer
    LastDebounceMode = millis();
    //Serial.println(VariableState);
  } 
  
  if ((millis() - LastDebounceMode) > debounceDelay) {
    // if the button state has changed:
    if (VariableRead != VariableState) {
      VariableState = VariableRead;
      if (VariableState == HIGH) {
        
        Mode=2;
        

      }
    }
  }
  LastVariableState = VariableRead;

  if (SelectedInputRead != LastSelectedInputRead) {              //Reading the state for the up Button
    // reset the debouncing timer
    LastDebounceSelectedInput = millis();
    //Serial.println(VariableState);
  } 
  
  if ((millis() - LastDebounceSelectedInput) > debounceDelay) {
    // if the button state has changed:
    if (SelectedInputRead != SelectedInputState) {
      SelectedInputState = SelectedInputRead;
      
      if (SelectedInputState == HIGH) {
        Mode = 0;

      }
    }
  }
  LastSelectedInputRead = SelectedInputRead;

  if (PulsesRead != LastPulsesState) {      //Reading the state for the Down Button
    // reset the debouncing timer
    LastDebouncePulses = millis();
    //Serial.println(VariableState);
  } 
  
  if ((millis() - LastDebouncePulses) > debounceDelay) {
    // if the button state has changed:
    if (PulsesRead != DownState) {
      DownState = PulsesRead;
      if (DownState == HIGH) {
        Mode = 1;
        
      }
    }
  }
  LastPulsesState = PulsesRead;

  
  
  
  if (Mode==1){               //Pulses mode 
    // read the state of the switch into a local variable
    CurrentTime = millis();
    //Serial.println(PercentageMosfet);

    FrequencyMosfet = round(map(analogRead(FrequencyPin),0,1023,2,60));
    AnalogPedal = map(round(analogRead(A3)),0,1024,0,255);
    DutyRead = (map(analogRead(DutyPin),0,1023,10,350));
    PercentageMosfet = DutyRead/1000;;
    PeriodMosfet = (1000/FrequencyMosfet);
    PWMValue = int(map(analogRead(PWMPin),0,1023,50,255));

    if (AnalogPedal>40){
      
      
      if (CurrentTime - StartOfPulses <= TimeForPulses/2){

        if(CurrentTime - PreviousTime >= PeriodMosfet){
          PreviousTime+=PeriodMosfet;
          analogWrite(MosfetPin, PWMValue);
        }
      
        if(CurrentTime - PreviousTime >= (PeriodMosfet*PercentageMosfet)) {
          analogWrite(MosfetPin, 0);
        }
      }
      else if(CurrentTime - StartOfPulses >= TimeForPulses){
        StartOfPulses=CurrentTime;
        
        analogWrite(MosfetPin,0);
      }
      else{
        analogWrite(MosfetPin,0);
      }
    }
    else{
      digitalWrite(MosfetPin,LOW);
      StartOfPulses=CurrentTime;
      
      //Serial.println(StartOfPulses);
    }
  }      //Finish mode 0 (Pulses in a second)
  
  if (Mode==0){                   //Power selected on the pedal
    CurrentTime = millis();
    
    FrequencyMosfet = map(analogRead(FrequencyPin),0,1023,2,60);
    AnalogPedal = map(round(analogRead(A3)),0,1024,0,255);
    //Serial.println(PercentageMosfet);
    DutyRead = (map(analogRead(DutyPin),0,1023,10,350));
    PercentageMosfet = DutyRead/1000;
    
    PeriodMosfet = (1000/FrequencyMosfet);
    
    if (AnalogPedal>40){
      if(CurrentTime - PreviousTime >= PeriodMosfet){
        PreviousTime+=PeriodMosfet;
        PWMValue = int(map(AnalogPedal,0,255,50,255));
        analogWrite(MosfetPin, PWMValue);

      }
    
      if(CurrentTime - PreviousTime >= (PeriodMosfet*PercentageMosfet)) {
        analogWrite(MosfetPin, 0);
      }
    }
    else{
      digitalWrite(MosfetPin,LOW);
      StartOfPulses=CurrentTime;
      PreviousTime=CurrentTime;
     
    }    
  }      //Finish mode 1 (Direct Potentiometer Mode)

  if (Mode==2){                   //Frequency selected on the pedal
    //CurrentTime = millis();
    AnalogPedal = analogRead(A3); //map(round(analogRead(A3)),0,1024,0,255);
    MaxFrequency = map(analogRead(FrequencyPin),0,1023,30,60);
    FrequencyMosfet = round(map(AnalogPedal,0,1023,0,MaxFrequency));
    PWMValue = int(map(analogRead(PWMPin),0,1023,50,255));
    
    PeriodMosfet = 1000/FrequencyMosfet;
    Correction = (map(analogRead(DutyPin),0,1023,1,10));  //The correction value is to accomodate different sizes of solenoid, it adjusts the curve of duty cycle up or down. Put two '/' at the begining if not using potentiometers and read line 240
    //Correction = 10 //If you are not using the potentiometer to correct the value, please test with differents values of the correction and uncomment (Remove the two '/' on the begining of the line)
    DutyRead = Correction*FrequencyMosfet + 4;
    PercentageMosfet = DutyRead/1000;
    if (AnalogPedal>20){
      if(millis() - PreviousTime >= PeriodMosfet){
        PreviousTime+=PeriodMosfet;
        analogWrite(MosfetPin, PWMValue);

      }
    
      if(millis() - PreviousTime >= (PeriodMosfet*PercentageMosfet)) {
        analogWrite(MosfetPin, 0);
      }
    }
    else{
      digitalWrite(MosfetPin,LOW);
      StartOfPulses=millis();
      PreviousTime=millis();
      
    }    
  }      //Finish mode 2 (Direct Frequency)


}      //Loop end

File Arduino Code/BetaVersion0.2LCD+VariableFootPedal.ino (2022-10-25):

#include <Wire.h> 
#include <LiquidCrystal_I2C.h>


//Assingning Analog Pins

const int FrequencyPin = 1;               //Pin that sets the maximun frequency (ANALOG)
const int PercentagePin = 2;              //Pin from percentage of the cycle that turns the solenoid on (ANALOG)

//Assigning digital Pins

const int SelectModePin = 2;              // Pin to select mode of action (DIGITAL)
const int UpButtonPin = 3;                //Pin to change the frequency UP on direct mode (DIGITAL)
const int DownButtonPin = 4;              //Pin to change the frequency Down on direct mode (DIGITAL)
const int MosfetPin = 9;                  // the number of the LED pin (DIGITAL)
const int DigitalFootPedalPin = 10;       //Pin of the foot pedal potentiometer (DIGITAL)


//Assigning variables

float PeriodMosfet  = 0;                  //Time between the impacts its a ratio between 1/frequency
float FrequencyMosfet = 1;                //Frequency in hertz of the impacts menas impacts per second
float PercentageMosfet = 5;              //Percentage of the cycle that turns the solenoid on
float FootPedal = 0;                      //State of the foot pedal
float AnalogPedal = 0;                    //Defines the analog value of the varible pedal
float TimeForPulses = 1000;               //Base time for pulses on pulse mode
float StartOfPulses;                      //Marker for start of pulses
int DirectFrequency=1;                  //Value for the frequency on direct mode

int Mode;                                 //Mode of action
int MosfetState = LOW;                    //Mosfet state for the action High means activated Low deactivated

int LastModeState = LOW;
int ModeState;
long LastDebounceMode = 0;                // the last time the output pin was toggled

int LastUpState = LOW;
int UpState;
long LastDebounceUp = 0;                              

int LastDownState = LOW;
int DownState;
long LastDebounceDown = 0;

long LastDebounceLCD = 0;


unsigned long CurrentTime = 0;
unsigned long PreviousTime = 0;


long debounceDelay = 50;                  // the debounce time; increase if the output flickers

LiquidCrystal_I2C lcd(0x27,20,4);  // set the LCD address to 0x27 for a 16 chars and 2 line display

void setup() {
  pinMode(SelectModePin, INPUT);          //Button to select the mode
  pinMode(UpButtonPin, INPUT);
  pinMode(MosfetPin, OUTPUT);             //Set solenoid pin as output to Mosfet
  pinMode(DigitalFootPedalPin, INPUT);    //Set the pedal input when pressed
  Serial.begin(115200);                   //Higher baudrate to get millis acuratelly

  //LCD Startup
  lcd.init();
  lcd.backlight();
  lcd.setCursor(0,0);
  lcd.print("Mode:");
  WriteOnLCD();
  }

void WriteOnLCD(){          //Function that will be called to write the information on the LCD

  lcd.setCursor(5,0);
  if (Mode==1){
    lcd.print("Pulses     ");
  }
  if(Mode==0){
    lcd.print("Potenti    ");
  }
  if(Mode==2){
    lcd.print("Direct    ");
  }
  lcd.setCursor(0,1);
  lcd.print("Freq:  ");
  lcd.setCursor(7,1);
  lcd.print(FrequencyMosfet);
  
  
}




void loop() {
  int ModeRead = digitalRead(SelectModePin);
  int UpRead = digitalRead(UpButtonPin);
  int DownRead = digitalRead(DownButtonPin);
  
  
  if (millis()>=LastDebounceLCD){
    LastDebounceLCD=millis()+5000;
    //WriteOnLCD();
  }


  if (ModeRead != LastModeState) {                  //Reading the state for the Mode Button, function to change the mode of the machine
    // reset the debouncing timer
    LastDebounceMode = millis();
    //Serial.println(ModeState);
  } 
  
  if ((millis() - LastDebounceMode) > debounceDelay) {
    // if the button state has changed:
    if (ModeRead != ModeState) {
      ModeState = ModeRead;
      if (ModeState == HIGH) {
        
        if (Mode<2){
          Mode+=1;
        }
        else {
          Mode=0;
        }
        
        StartOfPulses=CurrentTime;
        PreviousTime=CurrentTime;
      }
    }
  }
  LastModeState = ModeRead;

  if (UpRead != LastUpState) {              //Reading the state for the up Button
    // reset the debouncing timer
    LastDebounceUp = millis();
    //Serial.println(ModeState);
  } 
  
  if ((millis() - LastDebounceUp) > debounceDelay) {
    // if the button state has changed:
    if (UpRead != UpState) {
      UpState = UpRead;
      
      if (UpState == HIGH) {
        
        if (DirectFrequency<=9){
          DirectFrequency+=1;
        }
        else if(DirectFrequency<=24){
          DirectFrequency+=5;
        }
        
      }
    }
  }
  LastUpState = UpRead;

  if (DownRead != LastDownState) {      //Reading the state for the Down Button
    // reset the debouncing timer
    LastDebounceDown = millis();
    //Serial.println(ModeState);
  } 
  
  if ((millis() - LastDebounceDown) > debounceDelay) {
    // if the button state has changed:
    if (DownRead != DownState) {
      DownState = DownRead;
      if (DownState == HIGH) {
        
        if (DirectFrequency>=11){
          DirectFrequency-=5;
        }
        else if(DirectFrequency>=2){
          DirectFrequency-=1;
        }
        
      }
    }
  }
  LastDownState = DownRead;

  
  
  
  if (Mode==1){               //Pulses mode 
    // read the state of the switch into a local variable
    CurrentTime = millis();
    //Serial.println(PercentageMosfet);

    FrequencyMosfet = map(analogRead(FrequencyPin),0,1023,1,50);
    AnalogPedal = map(round(analogRead(A3)),0,1024,0,100);
    float DutyRead = (map(analogRead(PercentagePin),0,1023,10,350));
    PercentageMosfet = DutyRead/1000;;

    
    
    PeriodMosfet = (1000/FrequencyMosfet);
    //Serial.println(PeriodMosfet);
    if (AnalogPedal>20){
      
      
      if (CurrentTime - StartOfPulses <= TimeForPulses/2){

        if(CurrentTime - PreviousTime >= PeriodMosfet){
          PreviousTime+=PeriodMosfet;
          if(MosfetState==LOW){
            MosfetState=HIGH;
            digitalWrite(MosfetPin, MosfetState);

          }
        }
      
        if(CurrentTime - PreviousTime >= (PeriodMosfet*PercentageMosfet)/100) {
          if(MosfetState==HIGH){
            MosfetState=LOW;
            digitalWrite(MosfetPin, MosfetState);
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

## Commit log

2021-06-25 Create Solenoid choice
2021-06-25 Update Solenoid choice
2021-06-25 Rename Solenoid choice to Solenoid choice.md
2021-06-25 Update Solenoid choice.md
2021-06-25 Rename Solenoid choice.md to Design Considerations/Solenoid choice.md
2023-03-20 Update README.md
    Updated diameter of the tube to be used with a better option, 3/8 inch 16g.
    Wrong tube dimension listed, it was listed 9/32 inches when it was supposed to be 5/16 inches.
    Changed wire diameter for the custom solenoid from 0.5 to 0.2mm.
2023-03-20 Create BetaVersion0.3LCD_NoPotentiometer
    Adding a version to the code that starts straight to the pedal frequency and the duty cycle based on an equation.
    This is based on experimental values and now the only thing to control is the limiting screw on the back of the handpiece.
2023-04-05 Create BetaVersion0.4_CorrectionForDifferentSolenoids
    This code will not habe harmonics on the vibration and with an 1335 solenoid now it's possible to engrave better and smoother.
2023-06-10 Add files via upload
    This replaces the buttons to select modes and optimizes the code to reduce harmonics in the handpiece. There are still 3 modes, the variable pedal, the selection on the potentiometers and the pulses mode (On for half second and off for half second). The digital button 2, when pressed, selects the variable pedal mode. The digital button 3, when pressed, selects the potentiometer selection mode. The digital button 4, when pressed, selects the pulses mode. The correction value for the variable pedal is the duty potentiometer (Analog input on pin A2).
    If no buttons or potentiometers are used here please read lines 239 and 240. The correction value should be tested. My opin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
    [BetaVersion0.4_ButtonSelectModes.ino]
2023-06-13 Update README.md
    Changed the voltage of the sugested solenoid.
2023-11-07 Update Solenoid choice.md
    Added the video on the description
2023-12-26 Delete CAD files/Box - Base of box.step
    The item does not fit the design.
    [Box - Base of box.step]
2023-12-26 Delete CAD files/Box - Lid.step
    The design does not fit the projected boards.
    [Box - Lid.step]
2023-12-26 Rename CAD files/Assembly new handpiece 1335.FCStd to CAD files/PreviousIdeas/Assembly new handpiece 1335.FCStd
    [Assembly new handpiece 1335.FCStd]
2023-12-26 Rename CAD files/Back Lid Part-Body.stl to CAD files/PreviousIdeas/Back Lid Part-Body.stl
    [Back Lid Part-Body.stl]
2023-12-26 Rename CAD files/Back Lid Part.FCStd to CAD files/PreviousIdeas/Back Lid Part.FCStd
    [Back Lid Part.FCStd]
2023-12-26 Rename CAD files/BackBody Part-Body.stl to CAD files/PreviousIdeas/BackBody Part-Body.stl
    [BackBody Part-Body.stl]
2023-12-26 Rename CAD files/BackBody Part.FCStd to CAD files/PreviousIdeas/BackBody Part.FCStd
    [BackBody Part.FCStd]
2023-12-26 Add files via upload
    Circuit boards of the controller and Arduino Nano based graver.
2023-12-26 Rename CAD files/Collet GRS.FCStd to CAD files/PreviousIdeas/Collet GRS.FCStd
    [Collet GRS.FCStd]
2023-12-26 Rename CAD files/Front cap-Body.stl to CAD files/PreviousIdeas/Front cap-Body.stl
    [Front cap-Body.stl]
2023-12-26 Rename CAD files/Front cap.FCStd to CAD files/PreviousIdeas/Front cap.FCStd
    [Front cap.FCStd]
2023-12-26 Rename CAD files/Screw cap-Body.stl to CAD files/PreviousIdeas/Screw cap-Body.stl
    [Screw cap-Body.stl]
2023-12-26 Rename CAD files/Screw cap.FCStd to CAD files/PreviousIdeas/Screw cap.FCStd
    [Screw cap.FCStd]
2023-12-26 Rename CAD files/Solenoid 1335.FCStd to CAD files/PreviousIdeas/Solenoid 1335.FCStd
    [Solenoid 1335.FCStd]
2023-12-26 Rename CAD files/Tube.FCStd to CAD files/PreviousIdeas/Tube.FCStd
    [Tube.FCStd]
2023-12-26 Rename Button board.png to Button board.png
2023-12-26 Change the custom board to Version 1
2023-12-26 Rename PCB Controll Board Simplified.png to PCBControllBoardSimplified.png
2023-12-26 Rename PCB Main Pannel Arduino Nano.png to PCBMainPannelArduinoNano.png
2023-12-26 Rename Schematic/Custom Board V2/PCBControllBoardSimplified.png to Pictures/PCBControllBoardSimplified.png
2023-12-26 Rename Schematic/Custom Board V2/PCBMainPannelArduinoNano.png to Pictures/PCBMainPannelArduinoNano.png
2023-12-26 Add files via upload
    The final version of the code for the Controll board V2.
2024-05-20 Uploading STEP files for ease of compatibility
    Answer to issue #1
    [Assembly new handpiece 1335.step, Back Lid Part-Body.step, BackBody Part-Body.step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]
2024-05-21 New gerber and arduino code
    Updates based on the issues applied
    [Button Pannel BOM.csv, Main Pannel BOM.csv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]
